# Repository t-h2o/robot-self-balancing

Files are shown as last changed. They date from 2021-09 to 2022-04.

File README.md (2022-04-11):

# robot-self-balancing

A self balancing robot made in [ETML](https://www.etml.ch/formations/automaticien.html)
was the final project of my CFC formation as automatician.

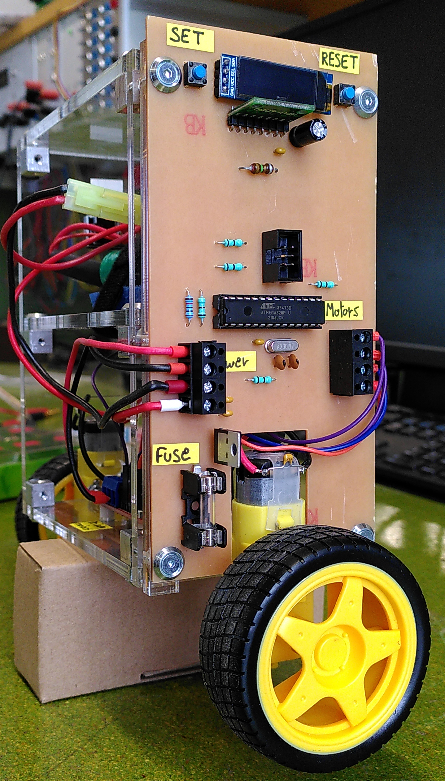
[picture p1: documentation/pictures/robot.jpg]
robot


## PCB

The pcb has been designed with [KiCad](https://en.wikipedia.org/wiki/KiCad).
A very nice open-source software !

### Schematic

<p align="middle">
<a href="electronic/plan/pcb-schematic.pdf">
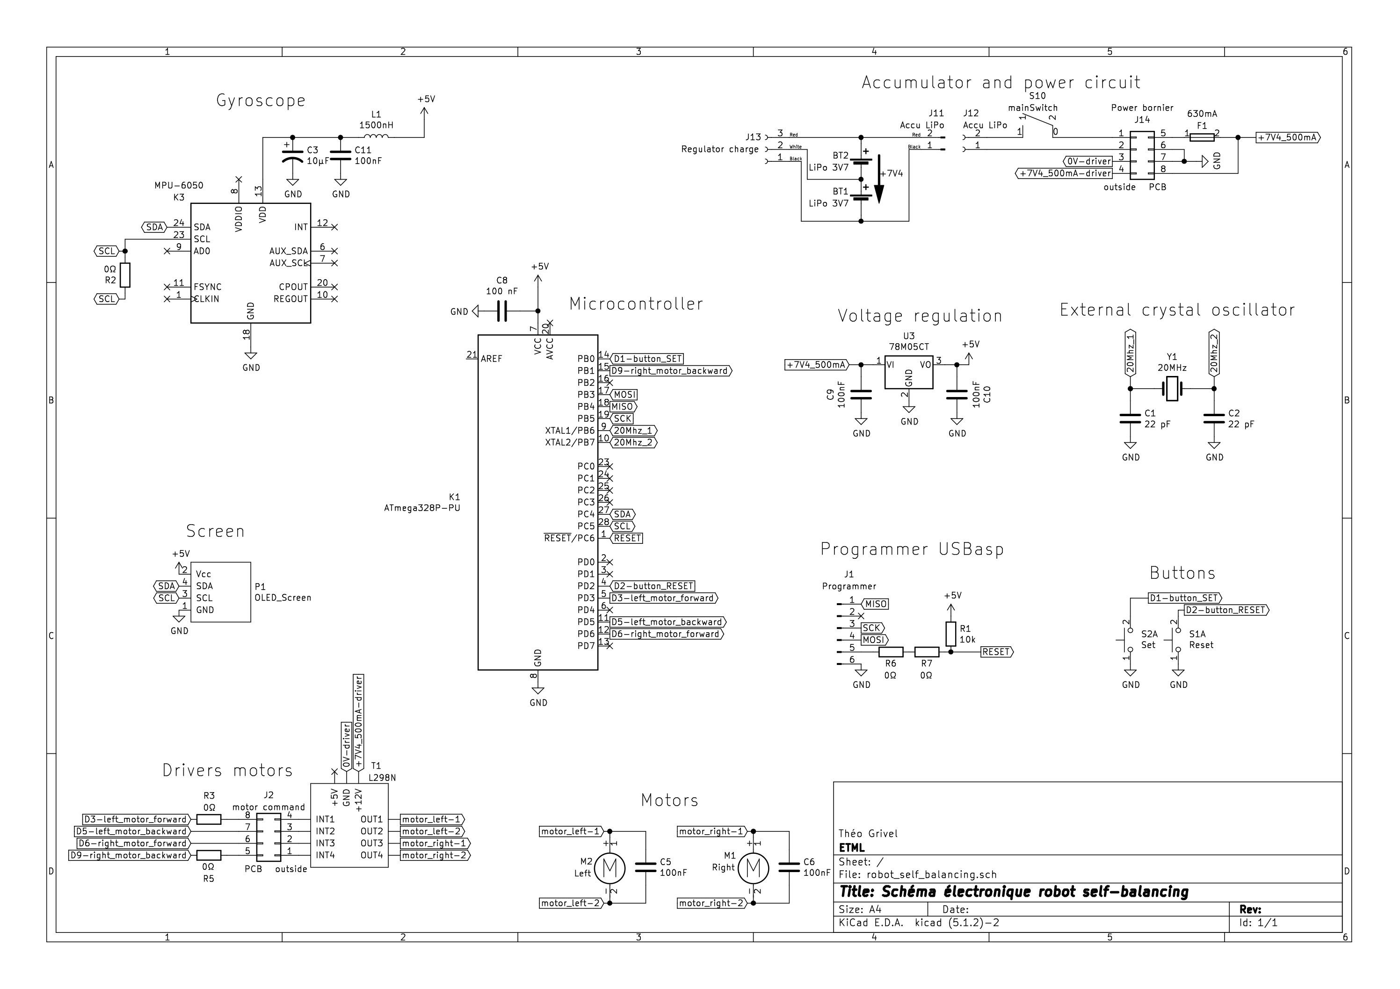
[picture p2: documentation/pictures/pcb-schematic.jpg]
Schematic image
</a></p>

### PCB

<p align="middle">
<a href="electronic/plan/pcb-root.pdf">
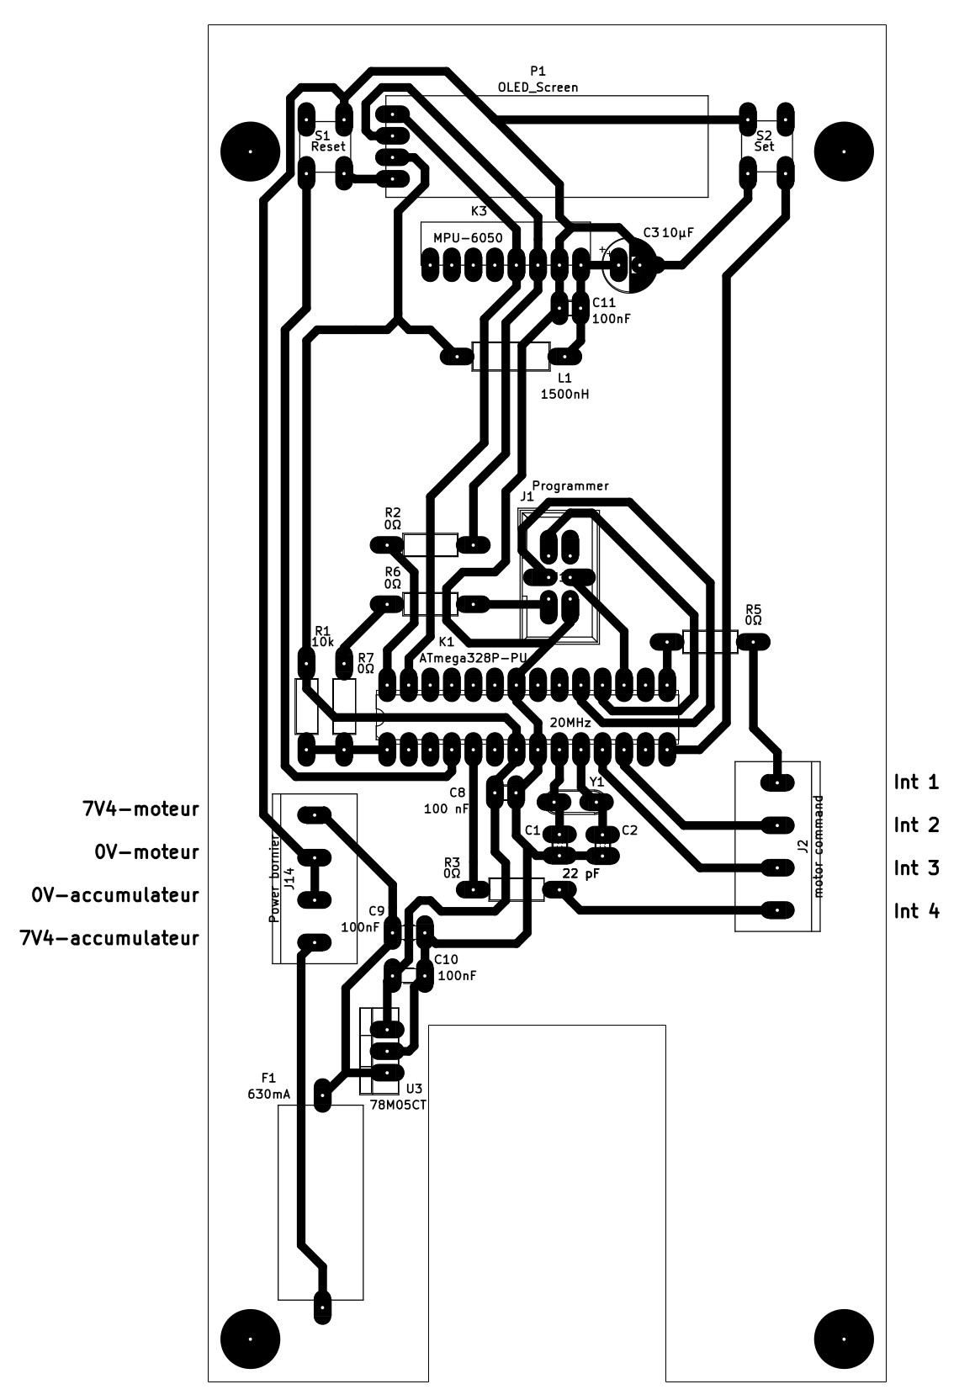
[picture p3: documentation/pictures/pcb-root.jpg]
root pcb image
</a></p>

## Mechanic

The mechanic design is made with [solid works](https://en.wikipedia.org/wiki/SolidWorks)

<p align="middle">
<a href="mechanic/plan/assembly.pdf">
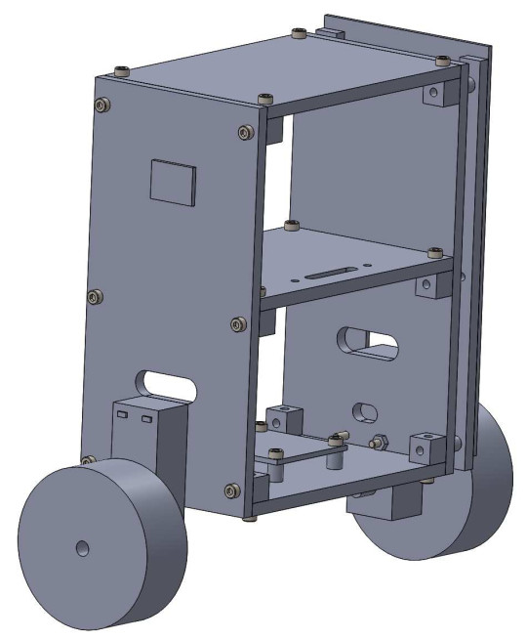
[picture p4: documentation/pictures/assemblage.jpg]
assembly image
</a></p>

## Software

To compile the [code](software/main.ino),
we need the [IDE Arduino](https://www.arduino.cc/en/software)

## In-details documentation could be found here

- [The requirements](documentation/partlist)
- [full documentation](documentation/documentation_robot_self_balancing_all.pdf)

## Ressources

- [French channel](https://www.youtube.com/channel/UCe3v5cVACw-5BKQOcwUaM8w)
- An other [Self-Balancing Robot](https://www.instructables.com/Arduino-Self-Balancing-Robot-1/)

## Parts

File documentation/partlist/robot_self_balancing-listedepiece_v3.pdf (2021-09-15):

file:///K:/AM/PROJETS/E/EnCours/TPI-TGL-Robot_Self_Balancing/01_Document_Technique/Liste_De_Piece/robot_self_balancing-ListeDePiece.ods 21.05.2021 / 15:58:51Page 1 / 1

### École Technique École des Métiers

Rue de Sébeillon 12 - CH 1004 Lausanne
Tél. 021 / 316 77 77 | Fax 021 / 316 77 00
Section : | Automatique | Lausanne, le 21.5.2021
Atelier : | E
Suivi par : | M.Darbellay
Nom du projet : Robot self-balancing

### Liste de pièces :

Pos. | Typ. | Qté. | Un. | N°. article | Désignation | Caractéristique | Réf. Fournisseur
1 | | 1 | | | Porte-fusible pour print | OGN RM25
2 | | 1 | | | Fusible | 630 mA / Rapide / d5 x 20
3 | | 5 | | | Résistance | 0 Ohms
4 | | 1 | | | Résistance | 10 kOhms
5 | | 1 | | | Inductance | 1500 nH
6 | | 1 | | | Régulateur 5V | 78M05CT
7 | | 2 | | | Bouton poussoir | 12V / 50mA / 1.6N
8 | | 2 | | | Condensateur céramique | 22pF / 100VDC 5 % / RM 2.5
9 | | 4 | | | Condensateur céramique | 100nF / 50V 10 % / RM 2.5
10 | | 1 | | | condensateur électrolytique | 10uF / 100VDC 20 % / RM 2.5
11 | | 1 | | | Bornier 2x3 pins
12 | | 1 | | SBC-Motodriver2 | Driver moteur | 25 W/ 12V | Joy-it
13 | | 2 | | COM-Motor01 | Moteur avec roues | 3-9V | Joy-it
14 | | 1 | | MPU-6050 | Gyroscope & accelerometer
15 | | 2 | | 250848 | Accumulateur Li-Ion | 3.7 V 1500 mAh | Conrad
16 | | 4 | | 300-42-827 | Barrette serre-fils 2 pôles noir | 250V/16A | Distrelec
17 | | 1 | | | Bouton power | 25T85
18 | | 1 | | | écran Oled | 128 x 32 pixels
19 | | 1 | | | Micro-contrôleur | Atmega328P-PU
20 | | 1 | | | Socle 28 pôles
21 | | 1 | | | plaque en cuivre pour PCB | 160 x 80
22 | | 1 | | | Quartz | 20 Mhz

Électronique

23 | 2 | PMMA | 160x10x5
24 | 3 | PMMA | 120x80x5
25 | 2 | PMMA | 160x80x5
26 | 1 | Aluminium | 144x10x10
27 | 4 | vis tête cylindrique 6 pans creux | M3 x 16
28 | 4 | vis tête cylindrique 6 pans creux | M3 x 16
29 | 4 | vis tête conique 90° 6 pans creux | M3 x 18
30 | 20 | vis tête conique 90° 6 pans creux | M3 x 8
31 | 24 | rondelle pour vis à tête conique | M3
32 | 8 | rondelle ressort | M3
33 | 8 | rondelle plate | M3
34 | 4 | écrou | M3
35 | 8 | entretoise plastique | M3 x 5

Mécanique

36 | 1 | | Fil flexible rouge | 350mm / 0.5 mm²
37 | 1 | | Fil flexible noir | 350mm / 0.5 mm²
38 | 1 | 227332 Cordon pour batterie | | 1.5 mm² | Conrad
39 | 2 | | cosse non isolé | 0.5-1.5 mm²
40 | 12 | | Cosse isolé | 0.5 mm²
41 | 1 | | Cosse isolé | 1 mm²
42 | 1 | | Cosse isolé | 1.5 mm²
43 | 4 | | fil arduino | 100 mm

Câblage

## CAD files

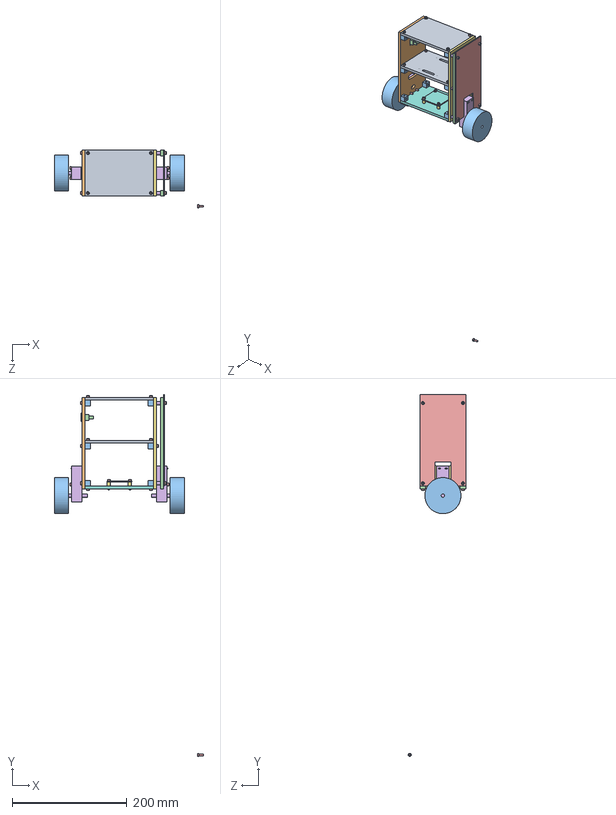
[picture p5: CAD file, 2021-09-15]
mechanic/Assemblage/robot-V3.SLDASM
260.6 x 631.9 x 100.7 mm
base-haut
lateral-Switch
cubeTaraude x 12
supportPCB x 2
PCB
motor_Wheel_V2 x 2
lateral-PCB
base-driverMotors
base-accu
Ecrou_M3
roue x 2
MainSwitchPower
socket head cap screw_am x 33
entretoise_PCB x 4
entretoise_DRIVER x 4
driver_motor

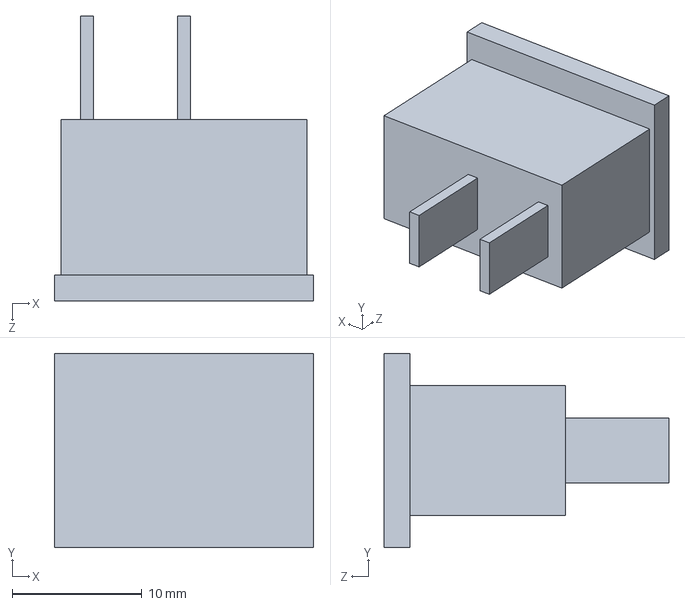
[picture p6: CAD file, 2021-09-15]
mechanic/Pieces/MainSwitchPower.SLDPRT
20.0 x 15.0 x 22.0 mm

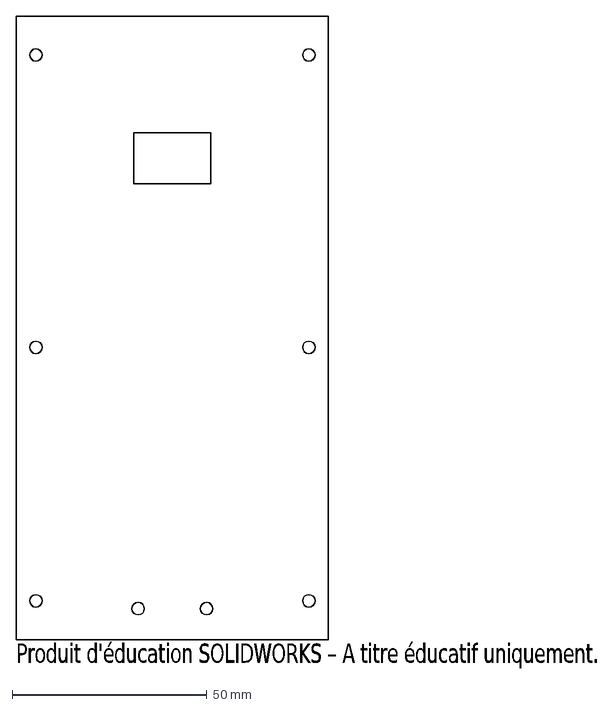
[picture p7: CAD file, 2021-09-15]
mechanic/dxf/lateral-Switch.DXF
Produit d'éducation SOLIDWORKS – A titre éducatif uniquement.

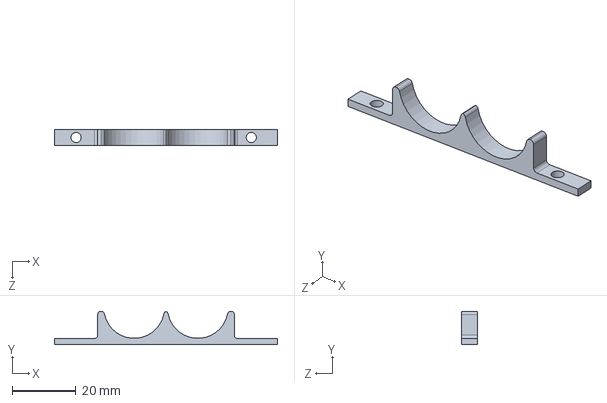
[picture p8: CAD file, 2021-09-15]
mechanic/Pieces/SupportAccuBas.SLDPRT
70.0 x 10.5 x 5.00 mm

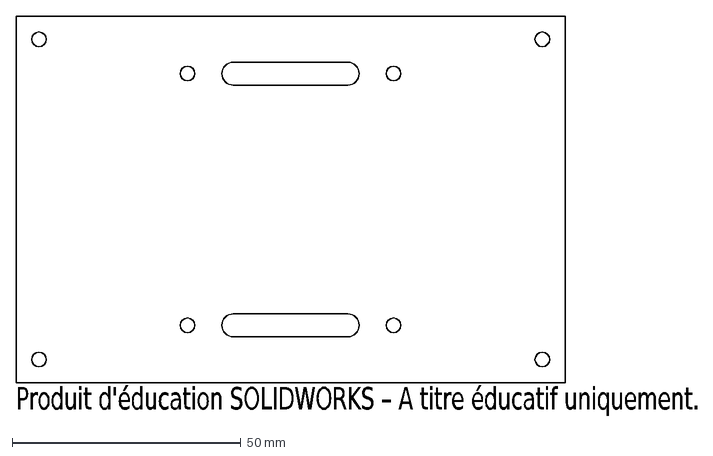
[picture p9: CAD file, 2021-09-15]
mechanic/dxf/base-accu.DXF
Produit d'éducation SOLIDWORKS – A titre éducatif uniquement.

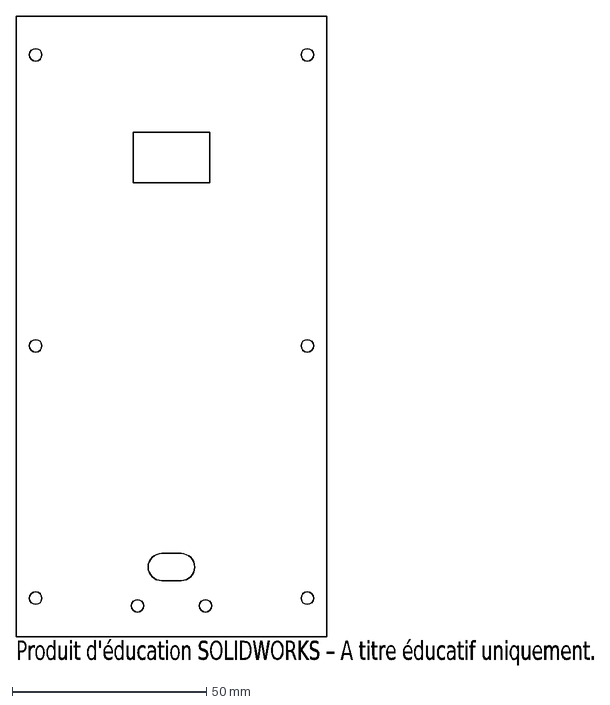
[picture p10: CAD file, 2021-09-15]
mechanic/dxf/lateral-Switch-RAINURE_MOTEUR.DXF
Produit d'éducation SOLIDWORKS – A titre éducatif uniquement.

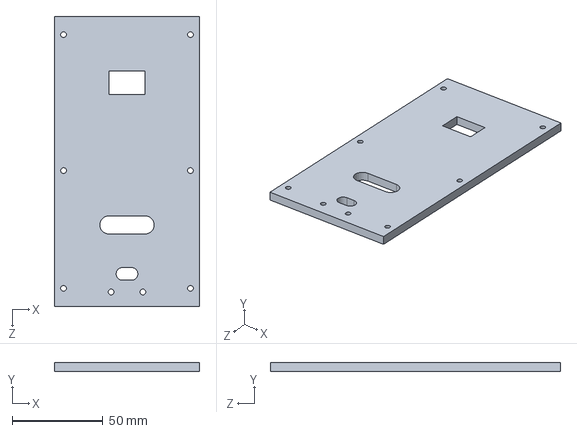
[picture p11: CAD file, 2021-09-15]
mechanic/Pieces/lateral-Switch.SLDPRT
80.0 x 5.00 x 160.0 mm

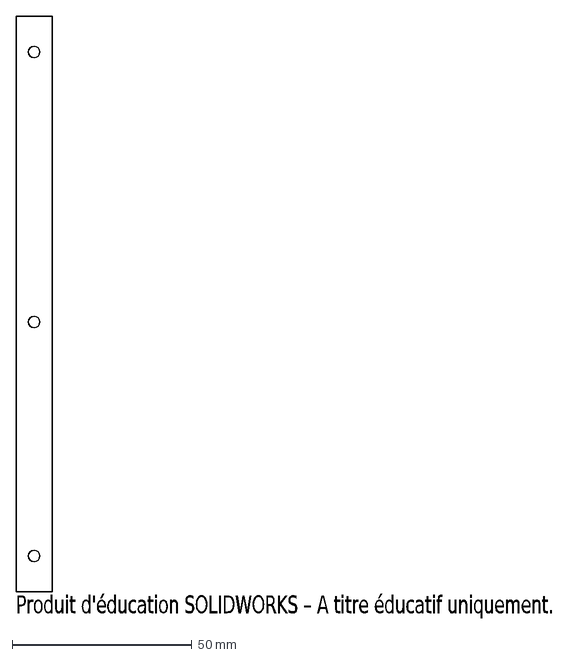
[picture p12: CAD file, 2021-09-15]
mechanic/dxf/supportPCB.DXF
Produit d'éducation SOLIDWORKS – A titre éducatif uniquement.

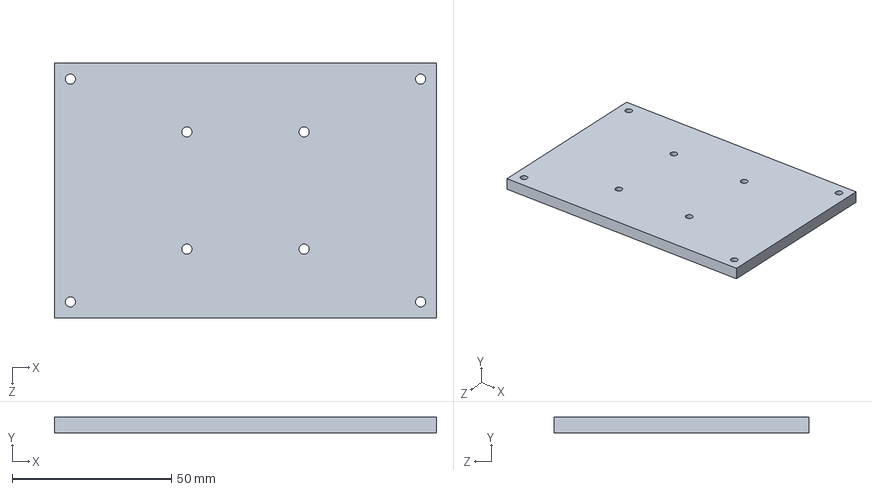
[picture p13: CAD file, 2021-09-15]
mechanic/Pieces/base-driverMotors.SLDPRT
120.0 x 5.00 x 80.0 mm

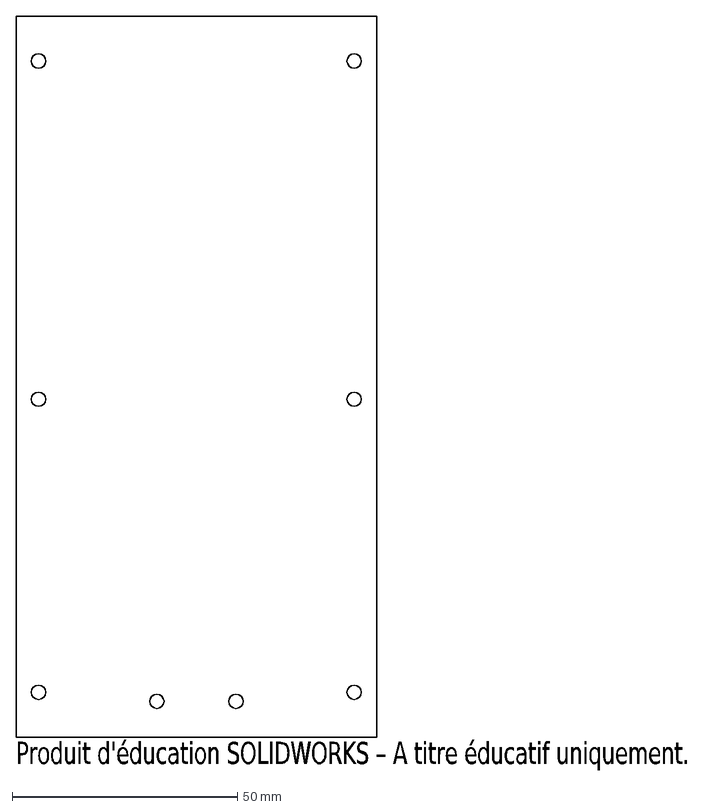
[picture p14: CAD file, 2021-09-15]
mechanic/dxf/lateral-PCB.DXF
Produit d'éducation SOLIDWORKS – A titre éducatif uniquement.

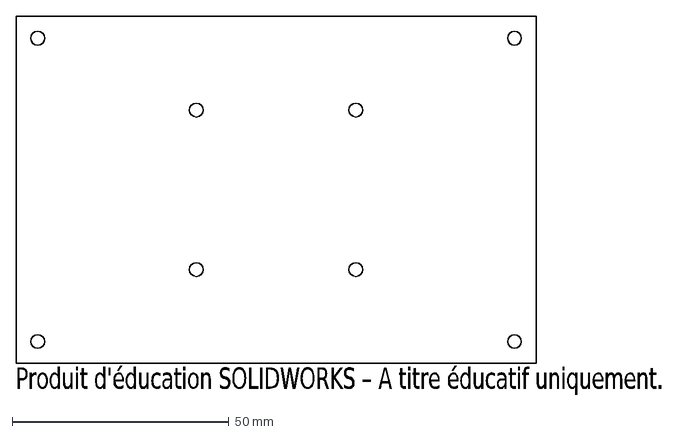
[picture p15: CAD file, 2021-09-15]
mechanic/dxf/base-driverMotors.DXF
Produit d'éducation SOLIDWORKS – A titre éducatif uniquement.

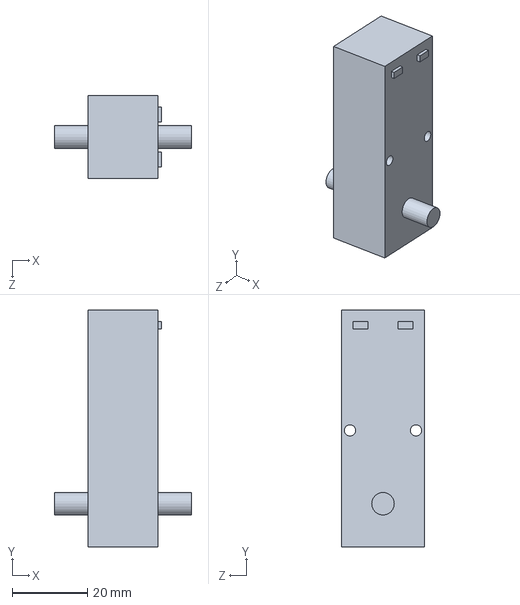
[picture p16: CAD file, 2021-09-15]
mechanic/Pieces/motor_Wheel_V2.SLDPRT
36.5 x 63.0 x 22.0 mm

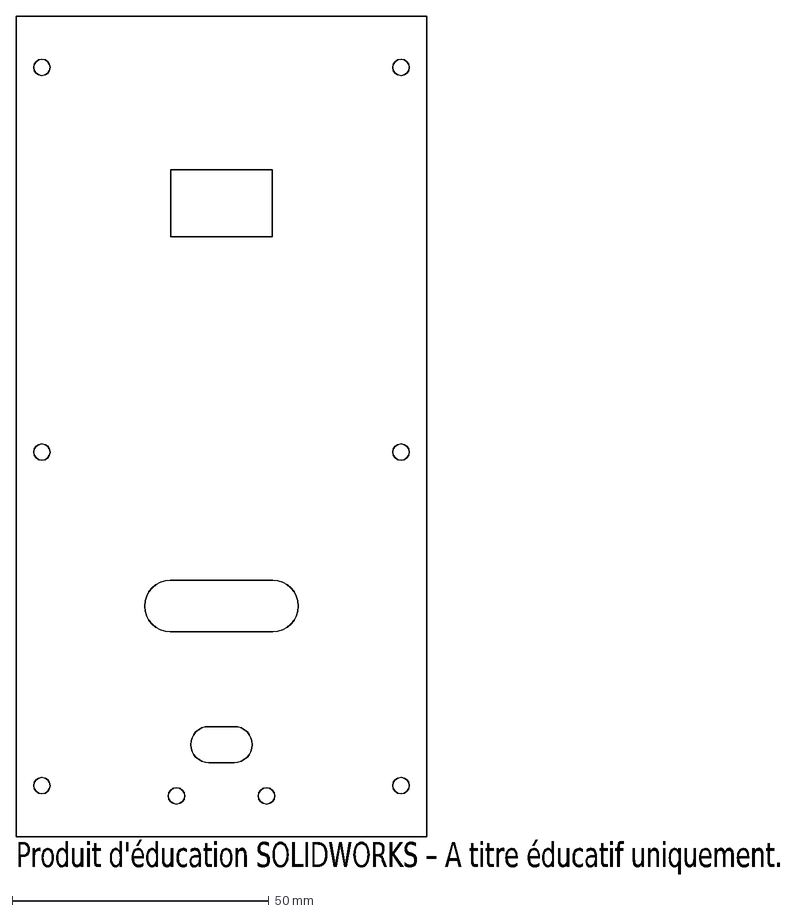
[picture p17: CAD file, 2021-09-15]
mechanic/dxf/lateral-Switch-V3-RAINUR_FIL.DXF
Produit d'éducation SOLIDWORKS – A titre éducatif uniquement.

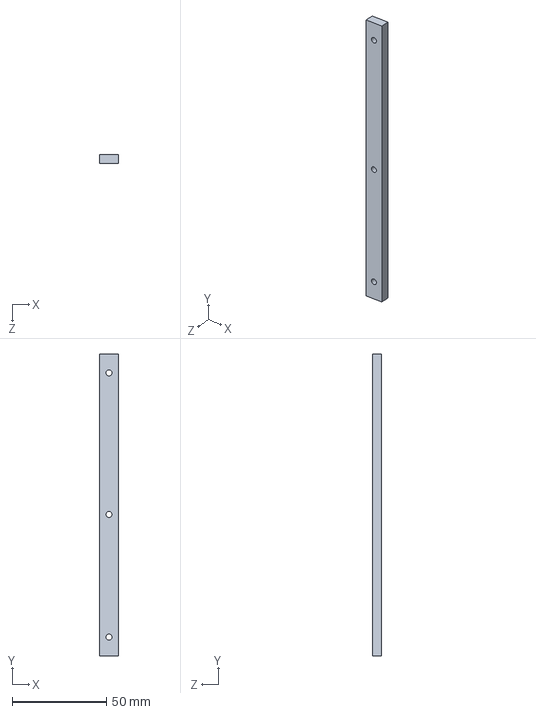
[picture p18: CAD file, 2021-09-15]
mechanic/Pieces/supportPCB.SLDPRT
10.0 x 160.0 x 5.00 mm

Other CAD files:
mechanic/Pieces/base-haut.SLDPRT
mechanic/dxf/base-haut.DXF
mechanic/Pieces/Ecrou_M3.SLDPRT
mechanic/Pieces/entretoise_DRIVER.SLDPRT
mechanic/Assemblage/robot-V0.SLDASM
mechanic/Assemblage/robot-V1.SLDASM
mechanic/Assemblage/robot-V2.SLDASM
mechanic/Assemblage/robot-V3 - Copie.SLDASM
mechanic/Mise_En_Plan/base-accu.SLDDRW
mechanic/Mise_En_Plan/base-driverMotors.SLDDRW
mechanic/Mise_En_Plan/base-haut.SLDDRW
mechanic/Mise_En_Plan/cubeTaraude.SLDDRW
mechanic/Mise_En_Plan/lateral-PCB.SLDDRW
mechanic/Mise_En_Plan/lateral-Switch.SLDDRW
mechanic/Pieces/PCB.SLDPRT
mechanic/Pieces/accumulateur.SLDPRT
mechanic/Pieces/base-accu.SLDPRT
mechanic/Pieces/cubeTaraude.SLDPRT
mechanic/Pieces/driver_motor.SLDPRT
mechanic/Pieces/entretoise_PCB.SLDPRT
mechanic/Pieces/lateral-PCB.SLDPRT
mechanic/Pieces/roue.SLDPRT

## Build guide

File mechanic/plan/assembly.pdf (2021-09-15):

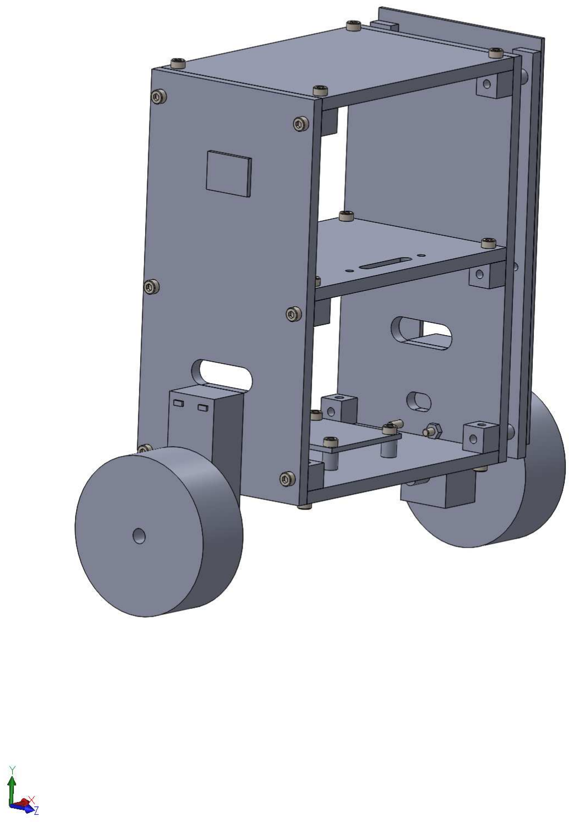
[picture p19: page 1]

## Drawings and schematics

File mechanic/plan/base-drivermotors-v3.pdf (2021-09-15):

# 36.8 t = 5mm

120

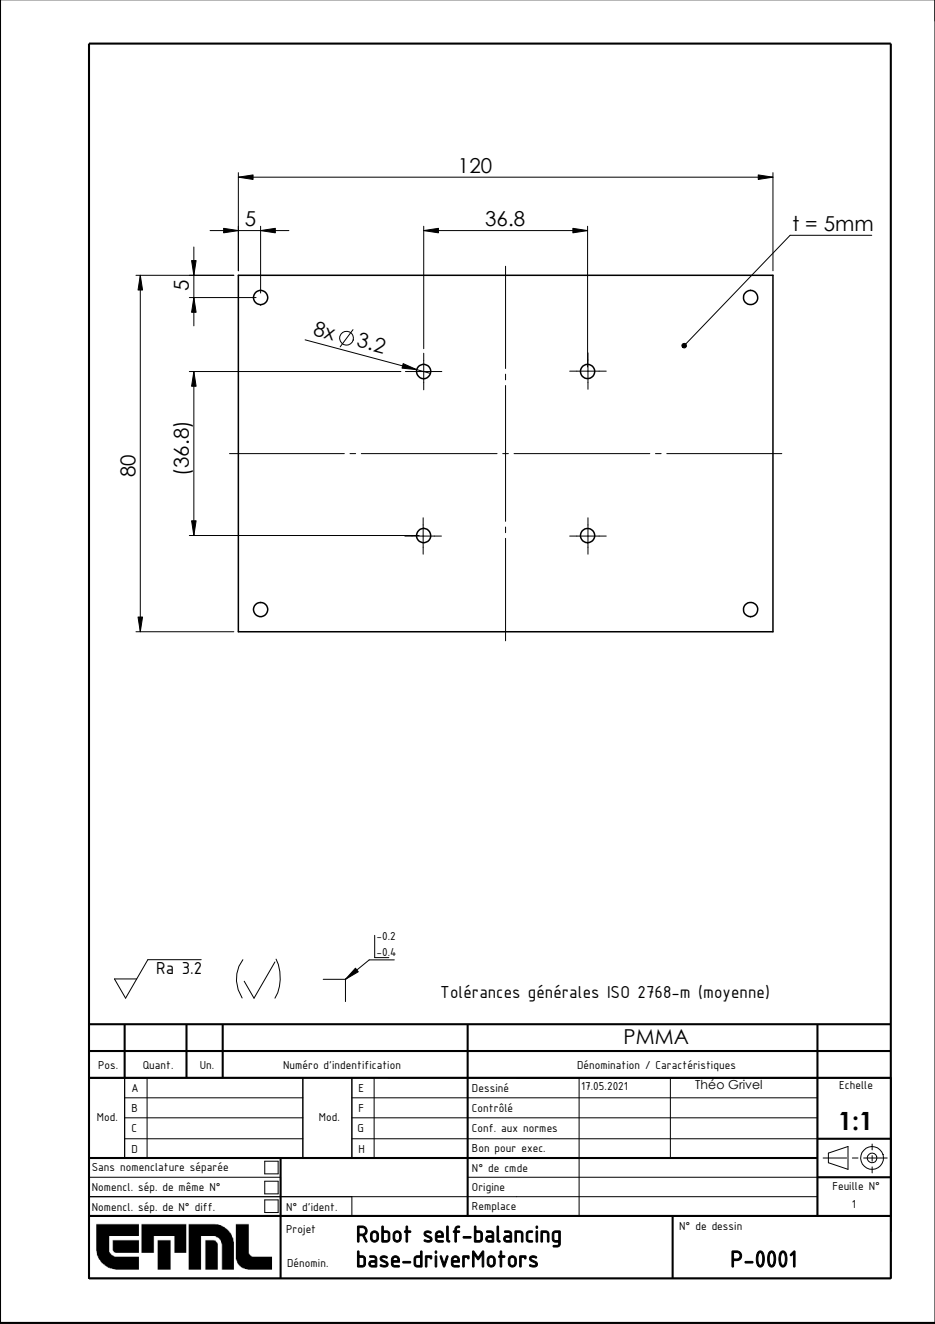
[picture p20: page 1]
Feuille N°; Origine

Tolérances générales ISO 2768-m (moyenne)

PMMA

Pos. | Quant. | Un. | Numéro d'indentification | Dénomination / Caractéristiques
Mod. | A | | Mod. | E | | Dessiné | 17.05.2021 | Théo Grivel | Echelle 1:1

B | | | F | | Contrôlé
C | | | G | | Conf. aux normes
D | | | H | | Bon pour exec.

Sans nomenclature séparée | | | N° de cmde

Nomencl. sép. de même N°

Nomencl. sép. de N° diff. | | N° d'ident. | Remplace

Projet Robot self-balancing base-driverMotors Dénomin. | N° de dessin P-0001

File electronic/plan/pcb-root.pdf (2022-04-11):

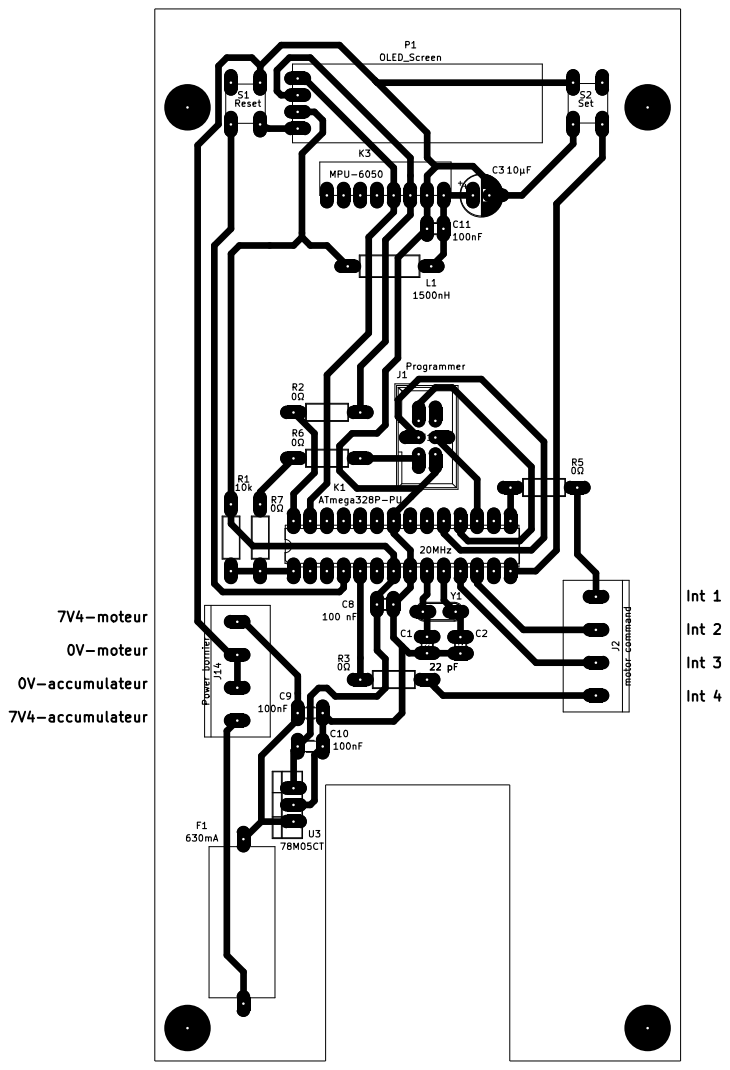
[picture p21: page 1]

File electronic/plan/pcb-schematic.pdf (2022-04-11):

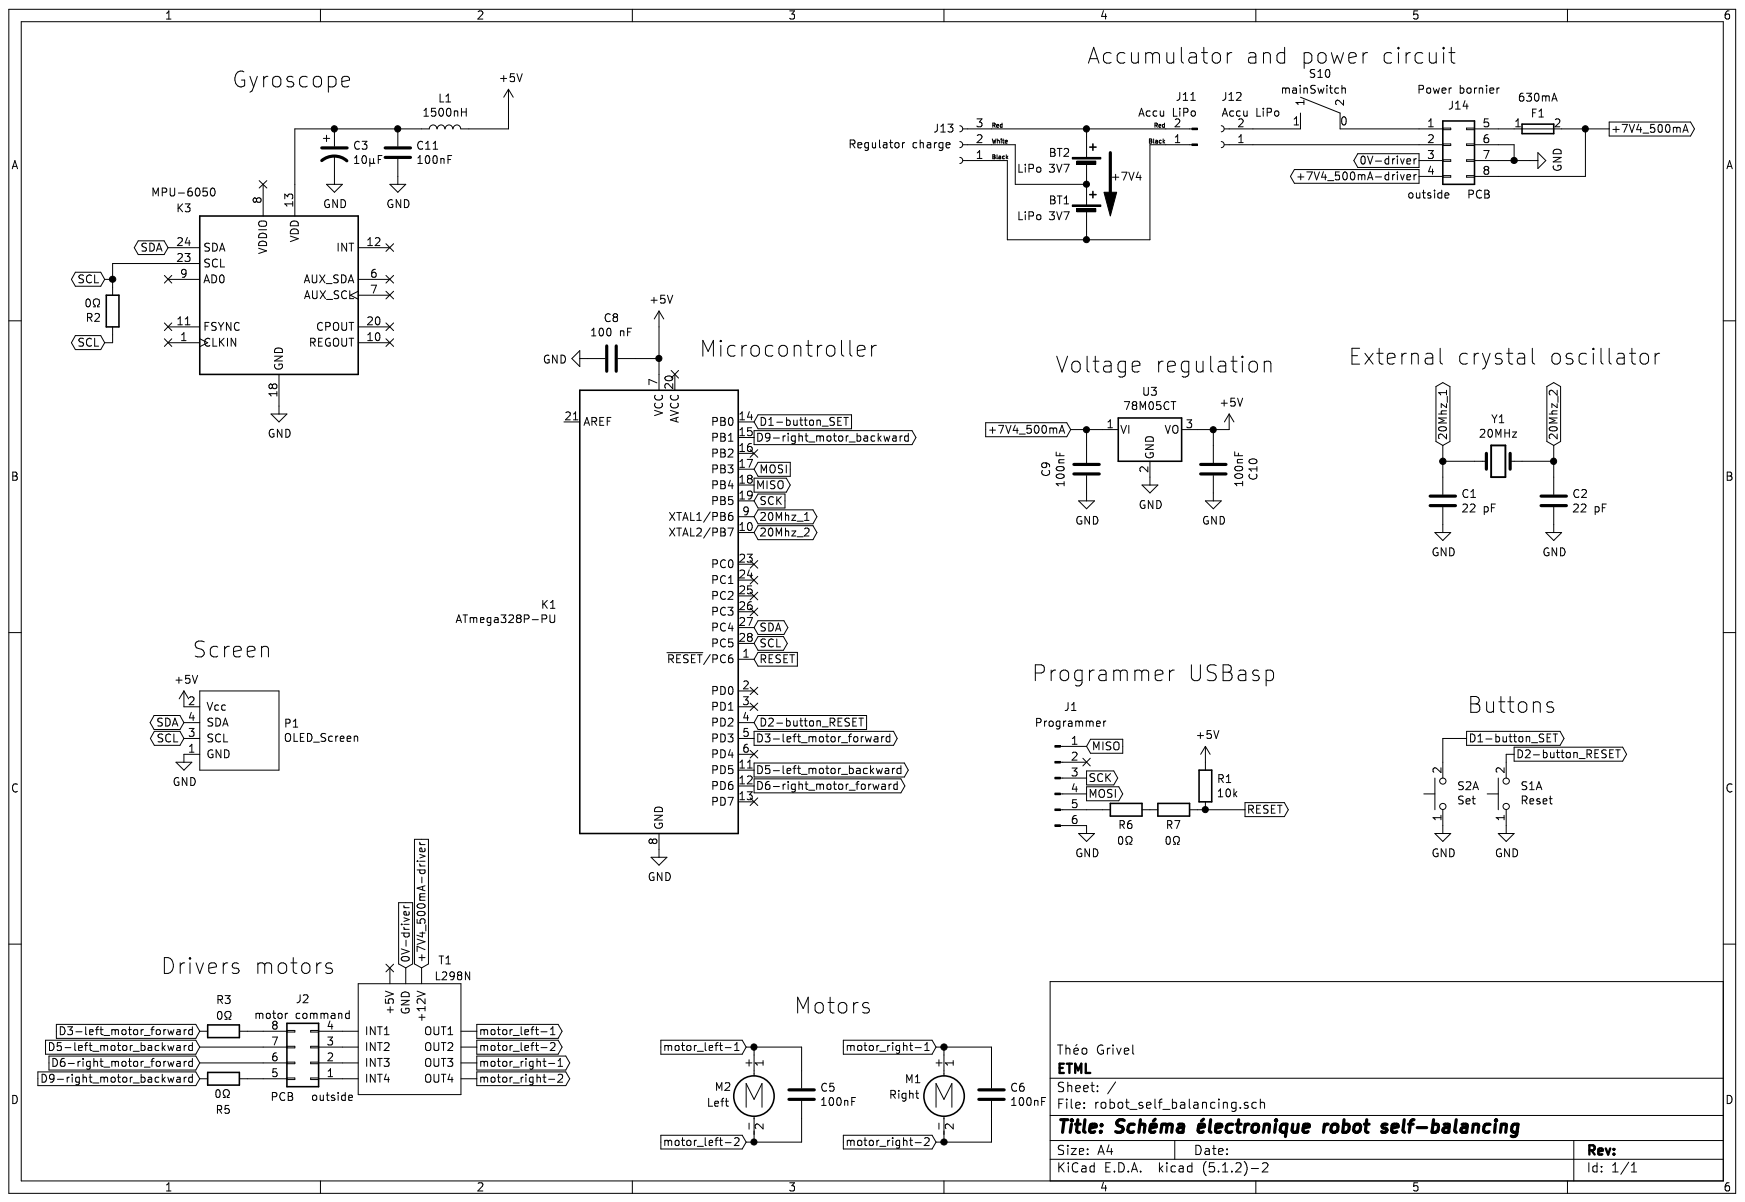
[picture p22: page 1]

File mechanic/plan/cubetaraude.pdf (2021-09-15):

10

10

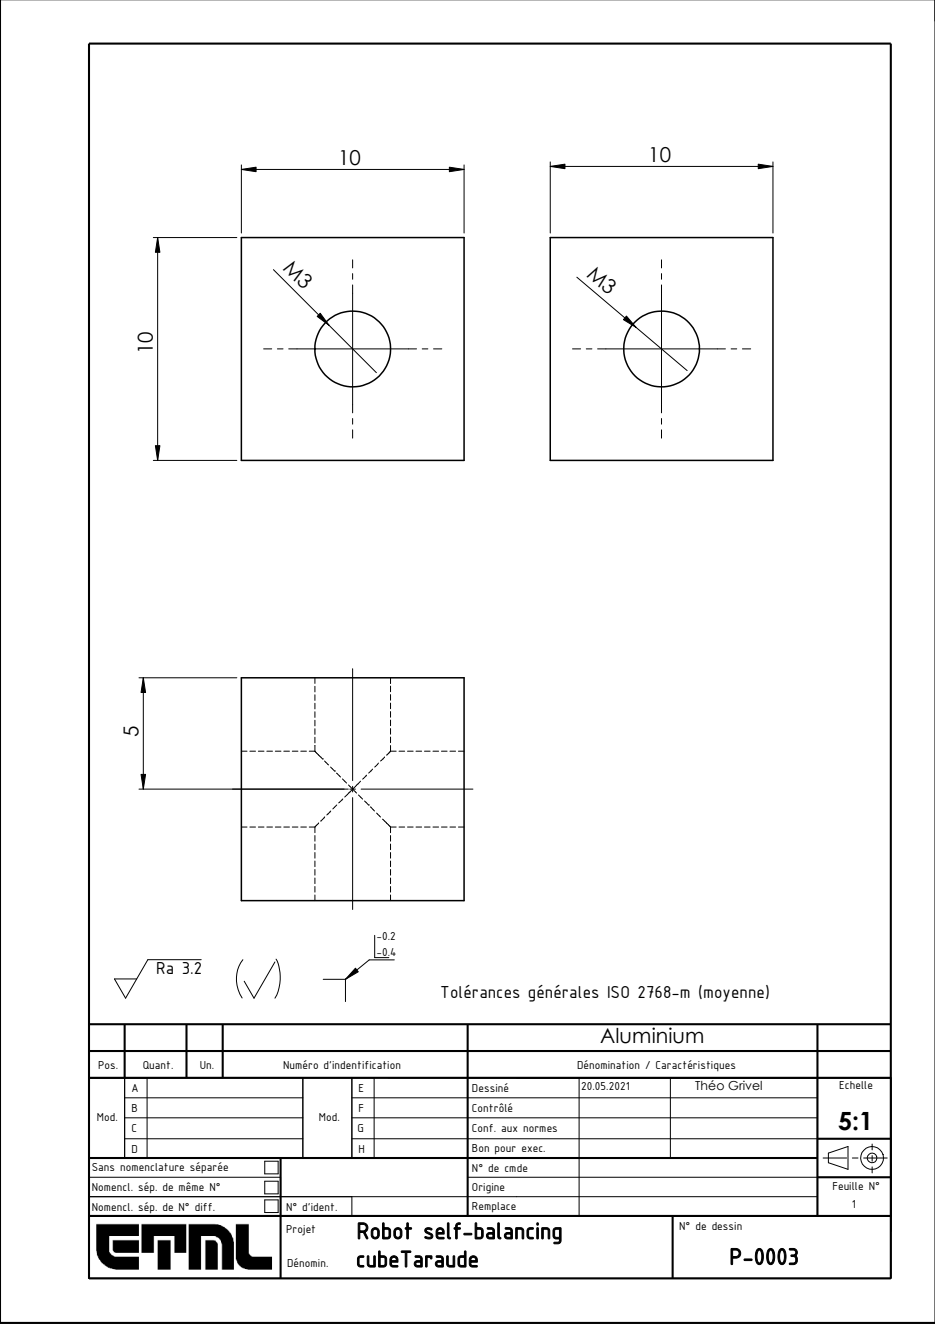
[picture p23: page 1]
Feuille N°; Origine

Tolérances générales ISO 2768-m (moyenne)

Aluminium

Pos. | Quant. | Un. | Numéro d'indentification | Dénomination / Caractéristiques
Mod. | A | | Mod. | E | | Dessiné | 20.05.2021 | Théo Grivel | Echelle 5:1

B | | | F | | Contrôlé
C | | | G | | Conf. aux normes
D | | | H | | Bon pour exec.

Sans nomenclature séparée | | | N° de cmde

Nomencl. sép. de même N°

Nomencl. sép. de N° diff. | | N° d'ident. | Remplace

Projet Robot self-balancing cubeTaraude Dénomin. | N° de dessin P-0003

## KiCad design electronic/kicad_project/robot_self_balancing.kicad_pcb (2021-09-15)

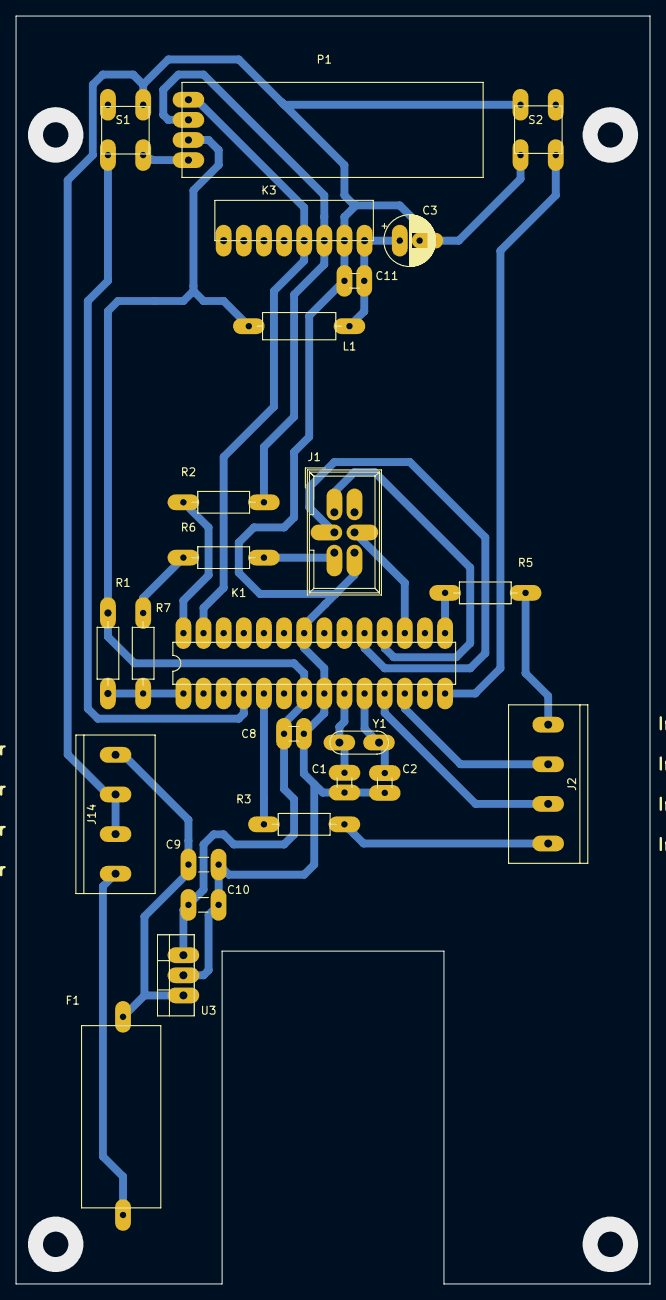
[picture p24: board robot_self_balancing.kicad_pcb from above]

Board: 2 copper layers, 80.0 x 160.0 mm, 37 parts (0 on the bottom side), 23 nets.

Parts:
7V4: +7V4; TGL-NO_PRINT
BT1, BT2: LiPo 3V7; TGL-NO_PRINT
C1, C2: 22 pF; TGL-C_12pF
C3: 10μF; CP_Radial_D6.3mm_P2.50mm
C5, C6: 100nF; TGL-NO_PRINT
C8: 100 nF; TGL-C_12pF
C9, C10, C11: 100nF; TGL-C_12pF
F1: 630mA; TGL-Fuse
J1: Programmer; TGL_IDC-Header_2x03_P2.54mm_Vertical_1.2
J2: motor command; TGL-Bornier4Pins_mm
J11, J12: Accu LiPo; TGL-NO_PRINT
J13: Regulator charge; TGL-NO_PRINT
J14: Power bornier; TGL-Bornier4Pins_mm
K1: ATmega328P-PU; TGL-ATmega328P_PU
K3: MPU-6050; TGL-MPU_6050-perpendiculaire
L1: 1500nH; TGL_L
M1: Right; TGL-NO_PRINT
M2: Left; TGL-NO_PRINT
P1: OLED_Screen; TGL-OLED_Screen
R1: 10k; R_Axial_DIN0207_L6.3mm_D2.5mm_P10.16mm_Horizontal
R2, R3, R5, R6, R7: 0Ω; TGL_R
S1: Reset; TGL-Push_Button
S2: Set; TGL-Push_Button
S10: mainSwitch; TGL-NO_PRINT
T1: L298N; TGL-NO_PRINT
U3: 78M05CT; TO-220-3_Vertical
Y1: 20MHz; Resonator-2Pin_W7.0mm_H2.5mm

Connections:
20Mhz_1: C1.1, K1.9, Y1.1
20Mhz_2: C2.1, K1.10, Y1.2
+5V: C8.2, C10.1, K1.7, L1.2, P1.2, R1.1, U3.3
+7V4_500mA: C9.2, F1.1, J14.8, U3.1
D1-button_SET: K1.14, S2.2
D2-button_RESET: K1.4, S1.2
D3-left_motor_forward: K1.5, R3.2
D5-left_motor_backward: J2.7, K1.11
D6-right_motor_forward: J2.6, K1.12
D9-right_motor_backward: K1.15, R5.1
GND: C1.2, C2.2, C3.2, C8.1, C9.1, C10.2, C11.2, J1.6, J14.6, J14.7, K1.8, K1.22, K3.18, P1.1, S1.1, S2.1, U3.2
MISO: J1.1, K1.18
MOSI: J1.4, K1.17
unnamed: C3.1, C11.1, K3.13, L1.1
unnamed: F1.2, J14.5
unnamed: J1.5, R6.1
unnamed: J2.5, R5.2
unnamed: J2.8, R3.1
unnamed: R6.2, R7.1
RESET: K1.1, R1.2, R7.2
SCK: J1.3, K1.19
SCL: K1.28, K3.23, P1.3, R2.1, R2.2
SDA: K1.27, K3.24, P1.4

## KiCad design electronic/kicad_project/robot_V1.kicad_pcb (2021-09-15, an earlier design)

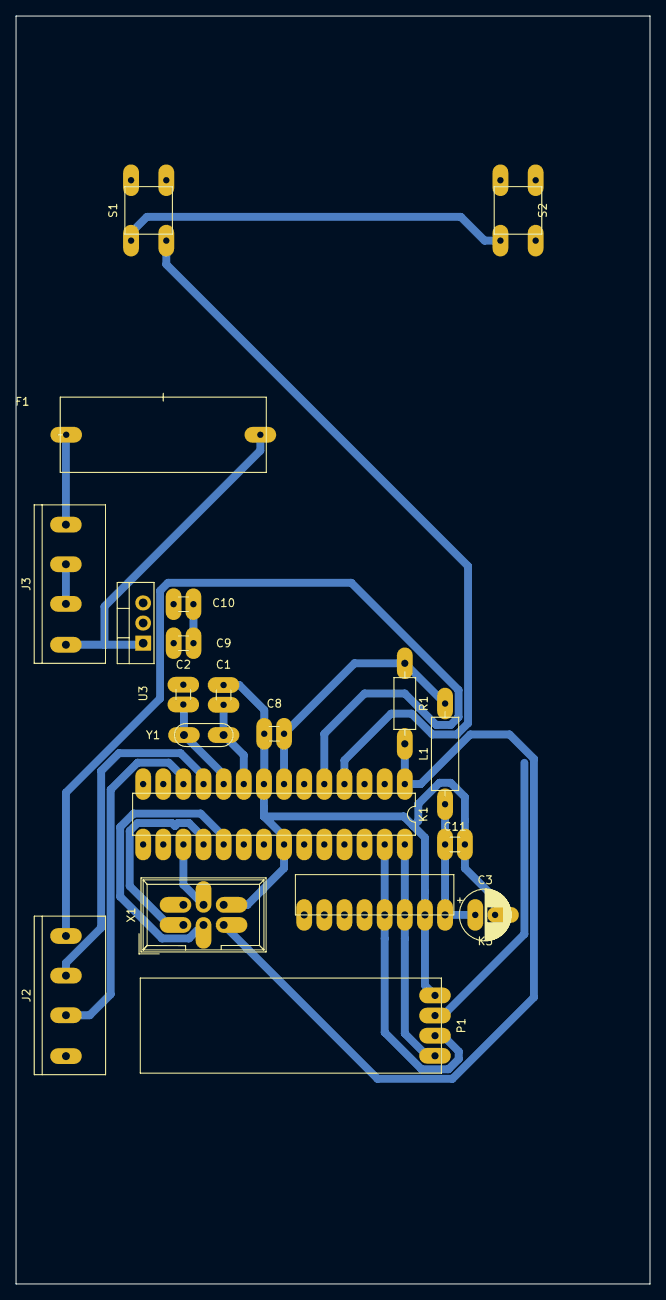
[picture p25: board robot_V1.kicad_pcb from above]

Board: 2 copper layers, 80.0 x 160.0 mm, 28 parts (0 on the bottom side), 20 nets.

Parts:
7V4: +7V4; TGL-NO_PRINT
BT1, BT2: LiPo 3V7; TGL-NO_PRINT
C1, C2: 22 pF; TGL-C_12pF
C3: 10uF; CP_Radial_D6.3mm_P2.50mm
C5, C6: 1 mF; TGL-NO_PRINT
C8: 100 nF; TGL-C_12pF
C9, C10, C11: 100nF; TGL-C_12pF
F1: 500mA; TGL-Fuse
J2: Motor commands; TGL-Bornier4Pins_mm
J3: Power bornier; TGL-Bornier4Pins_mm
K1: ATmega328P-PU; TGL-ATmega328P_PU
K3: MPU-6050; TGL-MPU_6050-perpendiculaire
L1: 330_Ohms/100MHz/300nH; TGL_L
M1: Right; TGL-NO_PRINT
M2: Left; TGL-NO_PRINT
P1: OLED_Screen; TGL-OLED_Screen
R1: 10k; R_Axial_DIN0207_L6.3mm_D2.5mm_P10.16mm_Horizontal
S1: Reset; TGL-Push_Button
S2: Set; TGL-Push_Button
S3: Main switch power; TGL-NO_PRINT
U3: LM7805_TO220; TO-220-3_Vertical
X1: Conn 2x03; TGL_IDC-Header_2x03_P2.54mm_Vertical_1.2
Y1: Crystal 20 Mhz; Resonator-2Pin_W7.0mm_H2.5mm

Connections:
20Mhz_1: C1.1, K1.9, Y1.1
20Mhz_2: C2.1, K1.10, Y1.2
+5V: C8.2, C10.1, K1.7, L1.2, P1.2, R1.1, U3.3
+7V4_500mA: C9.2, F1.1, J3.8, U3.1
D1-button_SET: K1.3, S2.2
D2-button_RESET: K1.4, S1.2
D3-left_motor_forward: J2.8, K1.5
D5-left_motor_backward: J2.7, K1.11
D6-right_motor_forward: J2.6, K1.12
D9-right_motor_backward: J2.5, K1.15
GND: C1.2, C2.2, C3.2, C8.1, C9.1, C10.2, C11.2, K1.8, K1.22, K3.18, P1.1, S1.1, S2.1, U3.2, X1.6
MISO: K1.18, X1.1
MOSI: K1.17, X1.4
unnamed: C3.1, C11.1, K3.13, L1.1
unnamed: F1.2, J3.5
unnamed: J3.6, J3.7
RESET: K1.1, R1.2, X1.5
SCK: K1.19, X1.3
SCL: K1.28, K3.23, P1.4
SDA: K1.27, K3.24, P1.3

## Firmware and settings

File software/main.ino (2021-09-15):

// Librairy
  #include <Adafruit_MPU6050.h>
  #include <Adafruit_SSD1306.h>
  #include <Adafruit_Sensor.h>
  #include <U8g2lib.h> // Dox sur la librairie de l'écran OLED : https://github.com/olikraus/u8g2/wiki/fntlistall  

  #include <Wire.h> // librairie pour le bus I2C

// Constante
  #define OFFSET_DEMARAGE_MOTEUR 90 // définit la valeur minimum où démarre le moteur
  #define TIME_BETWEEN_SCREEN 500 // Temps entre chaque fenêtre
  #define DELAY_ANTI_REBOUND 10000 // Temps anti rebond [us]

// Boutons Set Reset
  #define PIN_SET 2 // broche du bouton set
  bool lastStateButton_SET = HIGH; // Valeur par défaut du bouton
  bool falling_SET = 0; // front montant
  uint32_t lastFalling_SET = 0; // retient le dernier front      

  #define PIN_RESET 8 // broche du bouton reset
  bool lastStateButton_RESET = HIGH;  // when the button isn't push; the value is HIGH
  bool falling_RESET = 0;             // give the falling button
  uint32_t lastFalling_RESET = 0;     // Record the time of the last falling
  const byte pinMotor[] = {3, 5, 9, 6};

// MPU-6050
  Adafruit_MPU6050 mpu;

  // Variable pour le capteur MPU-6050
  int gyro_x, gyro_y, gyro_z;
  long gyro_x_cal, gyro_y_cal, gyro_z_cal;
  boolean set_gyro_angles;

  long acc_x, acc_y, acc_z, acc_total_vector;
  float angle_roll_acc, angle_pitch_acc;

  float angle_pitch, angle_roll, angle_axisZ;
  int angle_pitch_buffer, angle_roll_buffer;
  float angle_pitch_output, angle_roll_output;
  
  
  // retient la dernière prise de mesure
  long loop_timer;
  

// Display counter  
  byte displaycount = 0;


// OLED screen
  U8G2_SSD1306_128X32_UNIVISION_F_HW_I2C u8g2(U8G2_R0);

// Régulation
  
  // Constante PID pour la régulation
  float kP = 20.0, kI = 0, kD = 0.0;
  char letter = 'P'; // lettre Afficher durant les réglages.
  
  // dérivé et intégrale
  float lastError = 0, integralError;



void setup() {

// push button
  // résistance de pull up interne
  pinMode(PIN_SET, INPUT_PULLUP);
  pinMode(PIN_RESET, INPUT_PULLUP);
  
//Start I2C
  Wire.begin(); 

//Setup the registers of the MPU-6050                                                       
  setup_mpu_6050_registers(); 

// police de l'écran oled
  u8g2.begin();
  u8g2.enableUTF8Print();
  u8g2.setFont(u8g2_font_8x13B_tf  );  // 8x13 pixel : définit la police : https://github.com/olikraus/u8g2/wiki/fntlistall
  
  HomeScreen(); BetweenScreen(); // écran d'acceuille
  
  TestPushButtonScreen(); BetweenScreen(); // écran pour tester les boutons
}



void loop() {

  DisplayXaxisMPUScreen(); BetweenScreen(); // Prise du zéro 

  ScreenKPsetting(); BetweenScreen(); // réglage de P
  
  ScreenKIsetting(); BetweenScreen(); // réglage de I

  ScreenKDsetting(); BetweenScreen(); // réglage de D
  
}



// Menu pour régler P
void ScreenKPsetting(void){

  do{
	  // lis l'état des boutons
    ReadPushButton();
	
	// lis l'angle du capteur
    loop_mpu_6050();
    
	// Affiche que l'on va régler P et l'angle
    u8g2.setCursor(0, 13); u8g2.print("Réglage de Kp"); 
    u8g2.setCursor(0, 30); u8g2.print("inc. :"); u8g2.print(angle_pitch_output);
    
	// recharge l'écran
    RefreshScreen();
    
  }while(lastStateButton_SET);
    
    letter = 'P';
  BetweenScreen();
  
  do{
    
    ReadPushButton();
    
    loop_mpu_6050();

    Regulation();
    
    if(falling_RESET){
		
      // incrément P à chaque appuie de Reset
      kP += 2.0;
      
    }
    
    
  }while(lastStateButton_SET);

  BetweenScreen();
  shutDownMotors(); // turn off all motors
  
  do{
    
    ReadPushButton();
    
	// Affiche la valeur de P
    u8g2.setCursor(0, 13); u8g2.print("Valeur de Kp :"); 
    u8g2.setCursor(0, 30); u8g2.print(kP);
    
    RefreshScreen();
    
  }while(lastStateButton_SET);

}



void ScreenKIsetting(void){

  do{
    ReadPushButton();

    loop_mpu_6050();
    
    u8g2.setCursor(0, 13); u8g2.print("Réglage de I"); 
    u8g2.setCursor(0, 30); u8g2.print("inc. :"); u8g2.print(angle_pitch_output);
    
    RefreshScreen();
    
  }while(lastStateButton_SET);

  letter = 'I';
  BetweenScreen();
  
  do{
    
    ReadPushButton();
    
    loop_mpu_6050();

    Regulation();
    
    if(falling_RESET){
      // each time reset button is pressed
      // increments Kp of 1 
      kI += 0.1;
      
    }
    
    
  }while(lastStateButton_SET);

  
  BetweenScreen();
  shutDownMotors(); // turn off all motors
  
  do{
    
    ReadPushButton();
    
    u8g2.setCursor(0, 13); u8g2.print("Valeur de I : "); 
    u8g2.setCursor(0, 32); u8g2.print(kI);
    
    RefreshScreen();
    
  }while(lastStateButton_SET);

}


void ScreenKDsetting(void){

  do{
    ReadPushButton();

    loop_mpu_6050();
    
    u8g2.setCursor(0, 13); u8g2.print("Réglage de Kd"); 
    u8g2.setCursor(0, 30); u8g2.print("inc. :"); u8g2.print(angle_pitch_output);
    
    RefreshScreen();
    
  }while(lastStateButton_SET);
   letter = 'D';
  BetweenScreen();
  
  do{
    
    ReadPushButton();
    
    loop_mpu_6050();

    Regulation();
    
    if(falling_RESET){
      // each time reset button is pressed
      // increments Kp of 1 
      kD += 0.01;
      
    }
    
    
  }while(lastStateButton_SET);

  BetweenScreen();
  shutDownMotors(); // turn off all motors
  
  do{
    
    ReadPushButton();
    
    u8g2.setCursor(0, 13); u8g2.print("Valeur de KD : "); 
    u8g2.setCursor(0, 32); u8g2.print(kD);
    
    RefreshScreen();
    
  }while(lastStateButton_SET);

}


void TestMotorsScreen(void){
  for(byte i=0; i<4; i++){
    for(byte j=0; j<255; j+=5){
      analogWrite(pinMotor[i], j);
      u8g2.setCursor(0, 13); u8g2.print("Moteur : "); u8g2.print(pinMotor[i]);
      u8g2.setCursor(0, 32); u8g2.print("Vitesse : "); u8g2.print(j);
      RefreshScreen();
      delay(250);
    }
    analogWrite(pinMotor[i], 0);
  }

  
  uint32_t t=millis();
  u8g2.setCursor(0, 13); u8g2.print("Reculer ");
  u8g2.setCursor(0, 32); u8g2.print("full pwr"); 
  RefreshScreen();
  
  while((millis() - 4000) < t){
    
    analogWrite(3, 255);
    analogWrite(9, 255);
    
  }
  
  shutDownMotors(); // turn off all motors
}



void TestPushButtonScreen(void){
  do {

    ReadPushButton();
    
	// valeur qui sont mise à 1 ou à 0 à chaque front descendant 
    static bool SET_OnOFF = 1, RESET_OnOFF = 0;
	
    if(falling_RESET){RESET_OnOFF = !RESET_OnOFF;}
    if(falling_SET){SET_OnOFF = !SET_OnOFF;}

    u8g2.setCursor(0, 13); 
    u8g2.print("  SET : "); u8g2.print(!lastStateButton_SET); 
    u8g2.print(" : "); u8g2.print(SET_OnOFF); 
    
    u8g2.setCursor(0, 32);
    u8g2.print("RESET : "); u8g2.print(!lastStateButton_RESET); 
    u8g2.print(" : "); u8g2.print(RESET_OnOFF); 
    
    RefreshScreen();
    
  }while(lastStateButton_RESET || lastStateButton_SET);
  
} // Function



void DisplayXaxisMPUScreen(){
  
  /* Affiche l'inclinaison
   * Si on presse sur Reset,
   * Il reprend le 0 avec 1000 mesures
   */
  do{ 
    
    ReadPushButton();

    loop_mpu_6050();

    if(falling_RESET){set_OFFSET_mpu_6050_registers();}
    u8g2.setCursor(0, 13); u8g2.print("R take offset"); 
    u8g2.setCursor(0, 30); u8g2.print("axis X : "); u8g2.println(angle_pitch_output);
    RefreshScreen();
    
  }while(lastStateButton_SET);
}



void set_OFFSET_mpu_6050_registers(){ 
  
  //Read the raw acc and gyro data from the MPU-6050 1000 times                                          
  for (int cal_int = 0; cal_int < 1000 ; cal_int ++){                  
    read_mpu_6050_data(); 
    //Add the gyro x offset to the gyro_x_cal variable                                            
    gyro_x_cal += gyro_x;
    //Add the gyro y offset to the gyro_y_cal variable                                              
    gyro_y_cal += gyro_y; 
    //Add the gyro z offset to the gyro_z_cal variable                                             
    gyro_z_cal += gyro_z; 
    //Delay 3us to have 250Hz for-loop                                             

    displaycount++;
    if (displaycount > 60) { 
      
      //Display a bar loading
      u8g2.setCursor(0, 13); u8g2.print("prise du zéro..."); 
      u8g2.setCursor(0, 30); u8g2.print("mesure n°"); u8g2.print(cal_int);
      RefreshScreen();
      
      displaycount=0;
    } 
    delay(3);                                                          
  }

  gyro_x_cal /= 1000;                                                 
  gyro_y_cal /= 1000;                                                 
  gyro_z_cal /= 1000;
  
  u8g2.setCursor(0, 13);
  u8g2.print("offset X : ");
  u8g2.println(gyro_x_cal);
  RefreshScreen();
  delay(500);
  
  // Init Timer 
  loop_timer = micros();   
}



void loop_mpu_6050(void){
  
  // Get data from MPU-6050
  read_mpu_6050_data();
     
  //Subtract the offset values from the raw gyro values
  gyro_x -= gyro_x_cal;                                                
  gyro_y -= gyro_y_cal;                                                
  gyro_z -= gyro_z_cal;                                                
         
  //Gyro angle calculations . Note 0.0000611 = 1 / (250Hz x 65.5)
  
  //Calculate the traveled pitch angle and add this to the angle_pitch variable
  angle_pitch += gyro_x * 0.0000611;  
  //Calculate the traveled roll angle and add this to the angle_roll variable
  //0.000001066 = 0.0000611 * (3.142(PI) / 180degr) The Arduino sin function is in radians                                
  angle_roll += gyro_y * 0.0000611; 
  
  //z axis
  angle_axisZ += gyro_z * 0.0000611; 
                                     
  //If the IMU has yawed transfer the roll angle to the pitch angle
  angle_pitch += angle_roll * sin(gyro_z * 0.000001066);
  //If the IMU has yawed transfer the pitch angle to the roll angle               
  angle_roll -= angle_pitch * sin(gyro_z * 0.000001066);               
  
  //Accelerometer angle calculations
  
  //Calculate the total accelerometer vector
  acc_total_vector = sqrt((acc_x*acc_x)+(acc_y*acc_y)+(acc_z*acc_z)); 
   
  //57.296 = 1 / (3.142 / 180) The Arduino asin function is in radians
  //Calculate the pitch angle
  angle_pitch_acc = asin((float)acc_y/acc_total_vector)* 57.296; 
  //Calculate the roll angle      
  angle_roll_acc = asin((float)acc_x/acc_total_vector)* -57.296;       
  
  //Accelerometer calibration value for pitch
  angle_pitch_acc -= 0.0;
  //Accelerometer calibration value for roll                                              
  angle_roll_acc -= 0.0;                                               

  if(set_gyro_angles){ 
  
  //If the IMU has been running 
  //Correct the drift of the gyro pitch angle with the accelerometer pitch angle                      
    angle_pitch = angle_pitch * 0.9996 + angle_pitch_acc * 0.0004; 
    //Correct the drift of the gyro roll angle with the accelerometer roll angle    
    angle_roll = angle_roll * 0.9996 + angle_roll_acc * 0.0004;        
  }
  else{ 
    //IMU has just started  
    //Set the gyro pitch angle equal to the accelerometer pitch angle                                                           
    angle_pitch = angle_pitch_acc;
    //Set the gyro roll angle equal to the accelerometer roll angle                                       
    angle_roll = angle_roll_acc;
    //Set the IMU started flag                                       
    set_gyro_angles = true;                                            
  }
  
  //To dampen the pitch and roll angles a complementary filter is used
  //Take 90% of the output pitch value and add 10% of the raw pitch value
  angle_pitch_output = angle_pitch_output * 0.9 + angle_pitch * 0.1; 
  //Take 90% of the output roll value and add 10% of the raw roll value 
  angle_roll_output = angle_roll_output * 0.9 + angle_roll * 0.1; 
  //Wait until the loop_timer reaches 4000us (250Hz) before starting the next loop  
  
  // Print to Serial Monitor   
  
 while(micros() - loop_timer < 4000); 
 //Reset the loop timer                                
 loop_timer = micros();
  
}



void setup_mpu_6050_registers(){

  //Activate the MPU-6050
  
  //Start communicating with the MPU-6050
  Wire.beginTransmission(0x68); 
  //Send the requested starting register                                       
  Wire.write(0x6B);  
  //Set the requested starting register                                                  
  Wire.write(0x00);
  //End the transmission                                                    
  Wire.endTransmission(); 
                                              
  //Configure the accelerometer (+/-8g)
  
  //Start communicating with the MPU-6050
  Wire.beginTransmission(0x68); 
  //Send the requested starting register                                       
  Wire.write(0x1C);   
  //Set the requested starting register                                                 
  Wire.write(0x10); 
  //End the transmission                                                   
  Wire.endTransmission(); 
                                              
  //Configure the gyro (500dps full scale)
  
  //Start communicating with the MPU-6050
  Wire.beginTransmission(0x68);
  //Send the requested starting register                                        
  Wire.write(0x1B);
  //Set the requested starting register                                                    
  Wire.write(0x08); 
  //End the transmission                                                  
  Wire.endTransmission(); 
                                              
}



void read_mpu_6050_data(){ 

	// boucle où les mesures sont prise au maximum à 250 Hz
  while((micros() - loop_timer) < 4000){
    ;
  }
  //Read the raw gyro and accelerometer data

  //Start communicating with the MPU-6050                                          
  Wire.beginTransmission(0x68);  
  //Send the requested starting register                                      
  Wire.write(0x3B);
  //End the transmission                                                    
  Wire.endTransmission(); 
  //Request 14 bytes from the MPU-6050                                  
  Wire.requestFrom(0x68,14);    
  //Wait until all the bytes are received                                       
  while(Wire.available() < 14);
  
  //Following statements left shift 8 bits, then bitwise OR.  
  //Turns two 8-bit values into one 16-bit value                                       
  acc_x = Wire.read()<<8|Wire.read();                                  
  acc_y = Wire.read()<<8|Wire.read();                                  
  acc_z = Wire.read()<<8|Wire.read();                                  
  int temp = Wire.read()<<8|Wire.read();                                   
  gyro_x = Wire.read()<<8|Wire.read();                                 
  gyro_y = Wire.read()<<8|Wire.read();                                 
  gyro_z = Wire.read()<<8|Wire.read();  

  loop_timer = micros();  
}




void Regulation(void){
  
  // calcule l'erreur
  float error = 0 - angle_pitch_output;
  
  //Calcule l'intégrale
  integralError += error;
  
  // Calcule le signal PWM à donner aux moteurs
  float commande = error * kP + (error - lastError) * kD + integralError* kI ;
  
  
// Reculer
  if(commande > 0.0){ 
    
  commande += OFFSET_DEMARAGE_MOTEUR; // La valeur de commande + la valeur minimale pour faire tourner le moteur
    if(commande > 255.0 ){commande = 255;}
    
    analogWrite(5, commande);
    analogWrite(6, commande);

// Avancer    
  } else {
    
    commande = OFFSET_DEMARAGE_MOTEUR - commande; // donne la valeur absolue de la commande
    if(commande > 255){commande = 255;}
    
    analogWrite(3, commande);
    analogWrite(9, commande);
    
  }
  
  // Retien l'ancienne erreur
  lastError = error;
  
}



void ReadPushButton(void){
  
  // Measures the state of the buttons
  
  bool stateButtonReset = digitalRead(PIN_RESET);
  
  // if button is not equal at last state 
  if (stateButtonReset != lastStateButton_RESET){

    // Record the moment t [us]
    uint32_t _micros = micros();
  
    // if the time is bigger than the delay
    if(_micros - lastFalling_RESET >= DELAY_ANTI_REBOUND){
      
      // if that only a falling and not a rising
      if(stateButtonReset == 0){
        falling_RESET = 1;
      }
    }
    // Record again the last change state
    //Serial.println(_micros);
    lastFalling_RESET = _micros;
  } else {
     falling_RESET = 0;
  }
  
  // retiens le dernier état du bouton
  lastStateButton_RESET = stateButtonReset; 


  
  bool stateButtonSet = digitalRead(PIN_SET);
  
  // if button is not equal at last state 
  if (stateButtonSet != lastStateButton_SET){

    // Record the moment t [us]
    uint32_t _micros = micros();
  
    // if the time is bigger than the delay
    if(_micros - lastFalling_SET >= DELAY_ANTI_REBOUND){
      
      // if that only a falling and not a rising
      if(stateButtonSet == 0){
        falling_SET = 1;
      }
    }
    // Record again the last change state
    //Serial.println(_micros);
    lastFalling_SET = _micros;
  } else {
     falling_SET = 0;
  }
  
  // retiens le dernier état du bouton
  lastStateButton_SET = stateButtonSet; 
  
}



void RefreshScreen(void){
  
  // recharge l'écran
  u8g2.sendBuffer();          
  u8g2.clearBuffer(); 
  
}



void shutDownMotors(void){
	
  // met tous les moteurs à zéro
  analogWrite(5, 0);
  analogWrite(6, 0);
  analogWrite(3, 0);
  analogWrite(9, 0);
  
}



void BetweenScreen(void){
  
  // retiens le temps où on commence cette fenêtre
  uint32_t time1=millis();
  
  // Si (maintenant - durée de la fênetre) < temps de départ 
  while (millis() - TIME_BETWEEN_SCREEN < (time1)){
  
    u8g2.setCursor(0, 13); u8g2.print("NEXT SCREEN...");
    u8g2.setCursor(0, 32); u8g2.print(millis()); u8g2.print(" < "); u8g2.print(time1);
    RefreshScreen(); // recharge l'écran
    
  }
	// Affiche la lettre de la régulation
    u8g2.setCursor(20, 13); u8g2.print(letter);
	// recharge l'écran
    RefreshScreen();
}



void HomeScreen(void){
  do {
  
	// lis l'état des boutons  
  ReadPushButton();
  
  // Affiche au milieu de l'écran le numéro de l'écran
  u8g2.setCursor(0, 21); 
  u8g2.print("Home screen :V14");   
  
  // Recharge l'écran
  RefreshScreen();
  
  // Dès que set vaut 0 (appuyé)
  // On sort de la boucle
  }while(lastStateButton_SET);
}
